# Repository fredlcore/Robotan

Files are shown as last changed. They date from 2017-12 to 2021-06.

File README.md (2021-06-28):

# Robotan
Die deutsche Version gibt es <A HREF="README_de.md">hier</A>.  

WiFi access to Zucchetti-based lawnmower robots (Ambrogio, Stiga, Herkules etc.)  
See a list of (partly still assumed) compatible robots <A HREF="Supported Models.md">here</A>.  
Some boards left over from a collective order are still available. Contact robotan (ät) code-it.de if you are interested (German or English).

<H2><A HREF="LICENSE.md">License</A></H2>
<H2><A HREF="Assembly Instructions.md">Building the Robotan board</A></H2>
<H2><A HREF="Installation.md">Installation</A></H2>
<H2><A HREF="Setup.md">Software Setup</A></H2>
<H2><A HREF="Configuration.md">Configuration</A></H2>
<H2><A HREF="Troubleshooting.md">Troubleshooting</A></H2>
<H2><A HREF="FAQ.md">Frequently Asked Questions (FAQ)</A></H2>

<B>Some screenshots:</B>  

<B>Web-based remote control:</B>

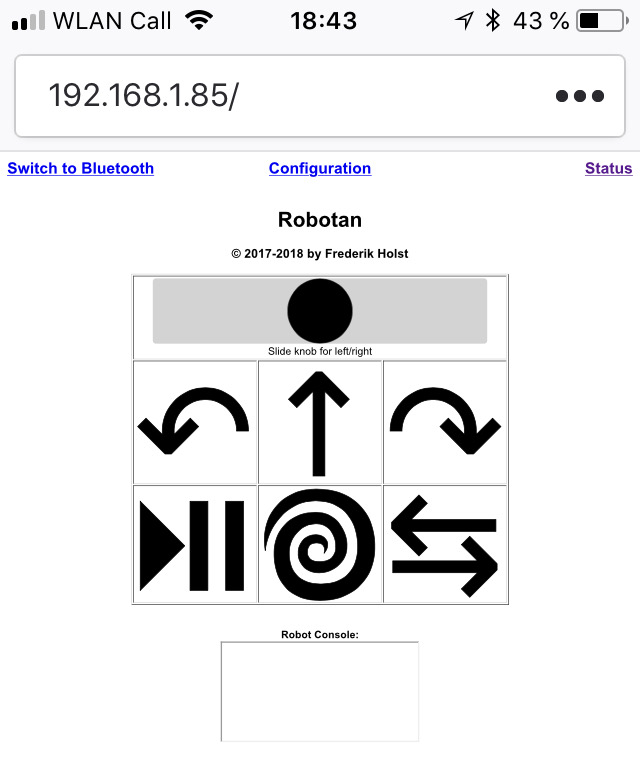
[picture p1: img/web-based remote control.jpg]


<B>Web interface with configuration and status information:</B>

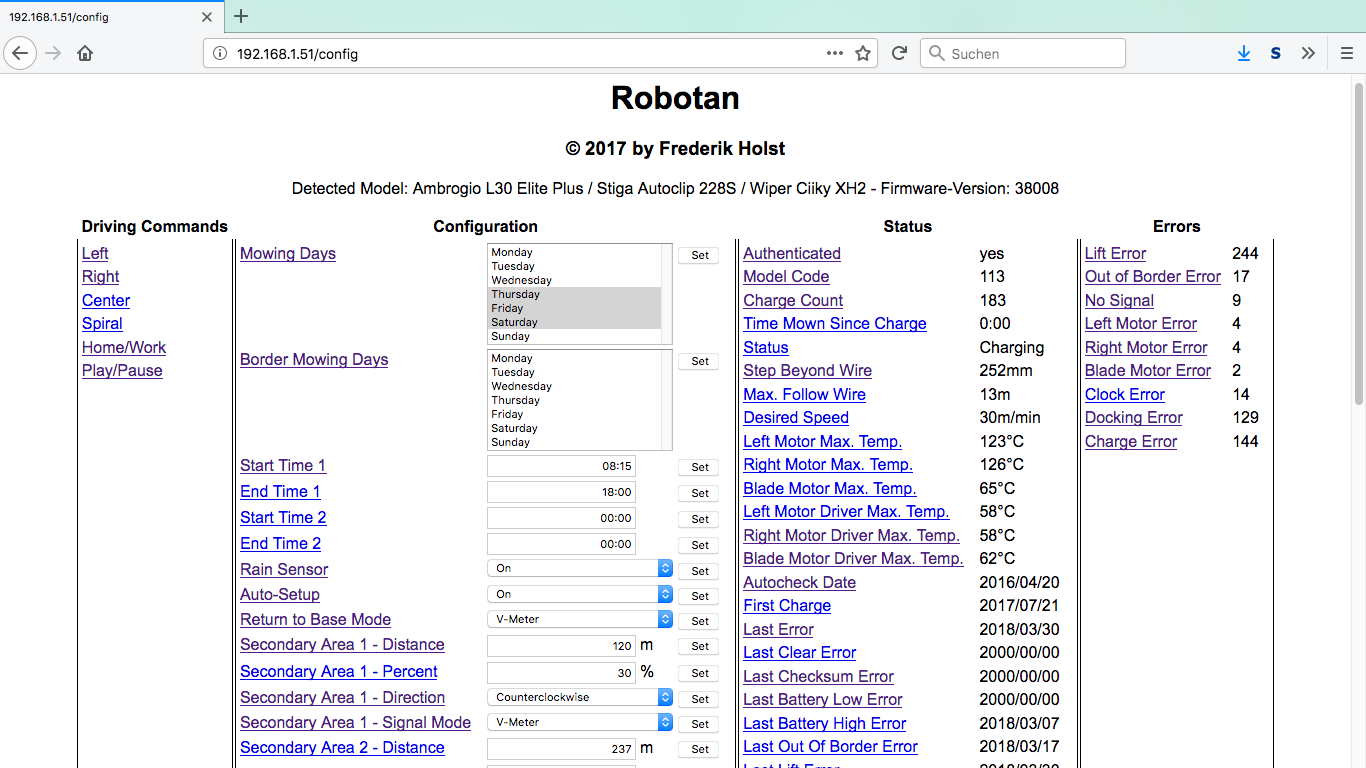
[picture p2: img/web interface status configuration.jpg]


<B>General settings (incl. GPS):</B>

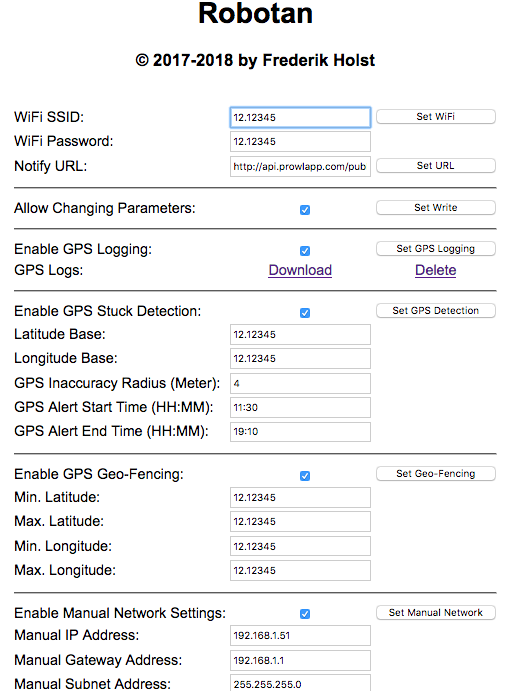
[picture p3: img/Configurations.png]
  

<B>Screencapture of realtime robot movements (new position polled every 10 seconds):</B>  
  
https://user-images.githubusercontent.com/24660955/123637079-e1455280-d81d-11eb-9b20-2d750a1a620e.mp4

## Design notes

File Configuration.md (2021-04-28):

<H2>Configuring Robotan</H2>
Die deutsche Version befindet sich <A HREF="Configuration_de.md">hier</A>.
<BR><BR>
To configure Robotan's options, go to<BR>
  <code>http://192.168.4.1/config</code>
<BR>
If you are asked for a login, the username is "Robotan" and the password is "Robotan88", unless you chose your own credentials during instalation.  
If Robotan is already connected to your own WiFi network, you'll have to use the IP address assigned to Robotan or try using the 
hostname "robotan" instead of the IP number. 
<H3>Configuring WiFi network</H3>
By default, Robotan sets up its own WiFi network called "Robotan" with the password "Robotan88". If you want to access your robot from 
within your own WiFi network, you can enter the name of your WiFi network at "WiFi SSID" and your WiFi's password at "WiFi Password".  
Then click on "Set WiFi" and wait a while. If your robot does not automatically connect to your own network, you can turn off the robot and
turn it on again after a few seconds.<BR>
<BR>
If Robotan cannot connect to your WiFi network, for example because the password is wrong or because it is too far away to pick up a signal, 
Robotan will fall back to setting up its own "Robotan" network mentioned above. However, it will try every five minutes to connect again to 
your WiFi network. This will ensure it will re-connect to your network even if it lost signal in a remote section of your garden.
<BR>
You also have the option to provide the Robotan module with a fixed IP address along with gateway, subnet and dns addresses in the configuration menu.

<H3>Configuring push notifications</H3>
Robotan can notify you in case the robot reports an error, for example when it gets stuck.  
To be able to send the notifications, Robotan must use your own WiFi network (see above). Robotan will call the URL defined at "Notify URL"
and add the reason for the notification (i.e. "Lift Error") at the very end, so you can call an URL and pass the reason as a parameter. If you don't want the error to be passed on, then just end your URL with a <code>#</code>. The reason text will still be appended, but the <code>#</code> will basically make the text being ignored in the URL.<BR>
<B>As of May 2020, only calls to https sites are supported!</B>
<H4>Example for using Prowl (Apple iPhone/iPad)</H4>
<A HREF="http://www.prowlapp.com">Prowl</A> is a notification app for iPhone and iPad. After you register, you can create an API key which 
you can send your notifications to. The URL for Robotan would look like this:<BR>
<code>https://api.prowlapp.com/publicapi/add?apikey=INSERT YOUR API KEY HERE&application=Robotan&event=</code>
<BR>
Take note of the end of the URL: The last parameter is "event=", so Robotan will add the reason for the notification there, so that the
final URL might end like "event=Lift Error"
<H4>Example for using SimplePush (Android)</H4>
<A HREF="http://www.simplepush.io">SimplePush</A> is a notification app for Android. After you've downloaded the app, you'll get a key which 
you can send your notifications to. The URL for Robotan would look like this:<BR>
<code>https://api.simplepush.io/send/INSERT YOUR KEY HERE/</code>. 
The error message will then be pushed to your Android device running the 
SimplePush app. Please take note that the URL must end with a <code>/</code>
after the key!
<BR>
<H4>Example for sending an e-mail via a PHP script</H4>
You can download and install the <A HREF="scripts/sendmail.php">sendmail.php script</A> on your own server and configure it to send an
e-mail through an e-mail service of your choice. Note: Only `https` addresses are supported!  
The script expects the parameter "error" to be sent via a GET request like this:<BR>
  <code>https://this-is-my-server.com/sendmail.php?error=Error-Message</code>
<BR>
Please make sure that the script runs smoothly before setting it up in Robotan by calling the script from your browser. If you receive
an e-mail from the script, you can use the URL in the Robotan configuration like this:
<BR>
  <code>https://this-is-my-server.com/sendmail.php?error=</code>
<BR>
Then click "Set URL" and Robotan will send out a notification each time an error occurs.

<H3>Configuring stuck detection</H3>
If you have installed a ADXL335 acceleration sensor, you can activate its use here which will provide a "stuck detection" for older robots who are not able to read the error status of the robot ("Steering only"). If you get false positives when the robot is mowing, play around with the sensitivity value a bit. Higher values lead to a greater tolerance, lesser values to a lower tolerance.

<H3>Configuring GPS functions</H3>
In the configuration menu, you have the following GPS-based options:  
<UL>
<LI>Enable GPS logging</LI>
GPS logs will be saved every 10 seconds into the device's flash memory until the size exceeds 1 MByte after which it will automatically be deleted. You have the option to download the logs in GPX format to be displayed for example on sites like <A HREF="http://www.gpsvisualizer.com/map_input">GPS Visualizer</A>.
<LI>Enable GPS stuck detection</LI>
This is useful for older robots which do not provide access to the error messages, like when the robot is stuck. This function will evaluate the (not 100% accurate) GPS position of the robot and determine whether the robot is stuck or not. The inaccuracy radius may help to prevent false positives. Alerts will only be sent during start and end time. Please note that these times are based on the UTC timezone (which is in summer two hours behind the rest of central Europe.  
The position of the base (garage) helps to prevent false positives when the robot is in the garage (and therefore looks as being 'stuck').  
<LI>Enable geo-fencing</LI>
You may provide coordinates of your garden here. Once the robot leaves these coordinates (e.g. because of theft) a message will be sent out with the current coordinates.
</UL>
<H3>GPIOs direct access</H3>
Via the URL <code>/gpio?x=y</code> the GPIO pins of the Wemos can be accessed directly, e.g. to control a relay shield, where <code>x</code> is the intenral number of the GPIO pin, and <code>y</code> is either 0 or 1, depending on whether the pin should be low or high.

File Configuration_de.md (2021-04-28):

<H2>Robotan konfigurieren</H2>
English version can be found <A HREF="Configuration.md">here</A>.
<BR><BR>
Um die Optionen von Robotan zu konfigurieren, ruft man folgende Adresse auf:
  `http://192.168.4.1/config`
<BR>
Wenn Du nach Zugangsdaten gefragt wirst, gib <code>Robotan</code> als Benutzernmane
und <code>Robotan88</code> als Passwort ein, wenn Du nicht bei der Installation Deine eigenen Zugangsdaten eingestellt hast. 
Falls Robotan bereits mit Deinem
WLAN-Netzwerk verbunden ist, musst Du die entsprechende IP-Adresse verwenden,
die Robotan zugewiesen wurde, oder den Hostnamen <code>robotan</code> statt
der IP-Adresse probieren.<BR>
<H3>WLAN-Netzwerk konfigurieren</H3>
Standardmäßig setzt Robotan sein eigenes WLAN-Netzwerk auf, das "Robotan" heißt 
und das Passwort <code>Robotan88</code> hat. Wenn Du Robotan aus Deinem eigenen
WLAN heraus erreichen möchtest, kannst Du den Namen des WLAN-Netzwerks unter
"WiFi SSID" und das WLAN-Passwort unter "WiFi Password" eingeben. Klicke dann
auf "Set WiFi" und warte einen Moment. Falls der Roboter sich nicht automatisch
mit Deinem WLAN verbindet, kannst Du den Roboter aus- und wieder anschalten.
Dann sollte er sich mit Deinem WLAN verbunden haben.
<BR><BR>
Falls Robotan sich nicht mit Deinem WLAN verbinden kann, weil z.B. das Passwort
falsch ist oder sich der Roboter außerhalb der WLAN-Reichweite befindet, wird
Robotan sein bereits erwähntes eigenes WLAN-Netzwerk "Robotan" aufspannen. Es
wird allerdings alle fünf Minuten probieren, sich wieder mit Deinem WLAN-Netzwerk
zu verbinden. Das gewährleistet, dass es sich wieder mit Deinem Netzwerk verbindet,
selbst wenn das Signal in einer entfernten Ecke Deines Gartens verloren gegangen
ist.<BR>  
Es gibt auch die Möglichkeit, dem Robotan-Modul im Konfigurationsmenü eine feste IP-Adresse, sowie Gateway-, Subnet- und DNS-Adressen zu vergeben.
<H3>Push Benachrichtigungen konfigurieren</H3>

Robotan kann Dich benachrichten, falls der Roboter einen Fehler aufweist, z.B.
wenn er sich festgefahren hat und angehoben werden muss.<BR>
Um Push-Benachrichtigungen versenden zu können, muss Robotan in Dein eigenes
WLAN eingebunden sein (s.o.). Robotan ruft im Falle eines Fehlers die URL auf,
die unter "Notify URL" angegeben ist und fügt dieser am Ende den Grund für die 
Meldung hinzu (z.B. "Lift Error" für den Fall, dass der Roboter feststeckt). 
Damit kann eine URL aufgerufen werden, die den Grund für die Meldung als Parameter
überträgt. Wenn Du nicht möchtest, dass die Fehlermeldung an das Script übertragen
wird, beende die URL einfach mit einem <code>#</code>. Der Grund für die Meldung
wird zwar weiterhin an die URL angehängt, aber das <code>#</code> sorgt dafür,
dass der Text nicht als Teil der URL interpretiert wird.<BR>
<B>Seit Mai 2020 sind nur noch Aufrufe von Seiten über https möglich!</B>

<H4>Beispiel: Benachrichtigung über Prowl (Apple iPhone/iPad)</H4>

<A HREF="http://www.prowlapp.com">Prowl</A> ist eine Benachrichtigungs App für
iPhone und iPad. Nachdem Du Dich dort registriert hast, kannst Du dort einen API
Schlüssel erzeigen, über den Du Benachrichtigungen an Dein Handy schicken kannst.
Die URL für Robotan würde folgendermaßen aussehen:<BR>
`https://api.prowlapp.com/publicapi/add?apikey=HIER DEN API SCHLÜSSEL EINTRAGEN&application=Robotan&event=`
<BR>
Beachte hierbei das Ende der URL: Der letzte Parameter ist "event=", woran 
Robotan den Benachrichtigungsgrund anhängen wird, so dass die endgülgtige URL
z.B. auf "event=Lift Error" enden könnte.

<H4>Beispiel: Benachrichtigung über SimplePush (Android)</H4>

<A HREF="http://www.simplepush.io">SimplePush</A> ist eine Benachrichtigungs App für
Android Geräte. Nachdem Du die App installiert hast, bekommst Du einen Schlüssel
angezeigt, über den Du Benachrichtigungen an Dein Handy schicken kannst.
Die URL für Robotan würde folgendermaßen aussehen:<BR>
`https://api.simplepush.io/send/HIER DEN SCHLÜSSEL EINTRAGEN/`
<BR>
Beachte hierbei das Ende der URL: Diese muss mit einem <code>/</code> hinter
dem Schlüssel enden!

<H4>Beispiel: E-Mail Versand über ein PHP Script</H4>

Du kannst das <A HREF="scripts/sendmail.php">sendmail.php script</A> auf Deinen
eigenen Server herunterladen und es so konfigurieren, dass es eine E-Mail über
einen E-Mail Server Deiner Wahl verschickt. Wichtig: Es werden nur Adressen mit `https` unterstützt!
Das Script erwartet den Parameter "error" über einen HTTP GET-Aufruf, z.B.
`https://this-is-my-server.com/sendmail.php?error=Error-Message`
<BR>
Bitte überprüfe, dass das Script fehlerfrei läuft, bevor Du es in Robotan 
einbindest, indem Du es vom Browser aus aufrufst. Wenn Du eine E-Mail von dem
Script erhälst, kannst Du die URL in der Robotan Konfiguration wie folgt 
einbinden:
<BR>
  `https://this-is-my-server.com/sendmail.php?error=`
<BR>
Dann klicke auf "Set URL" und Robotan wird jedes Mal, wenn ein Fehler auftritt,
eine Benachrichtigung versenden.

<H3>Stillstandserkennung konfigurieren (für ältere Roboter)</H3>
Wenn ein ADXL335 Beschleunigungssensor installiert ist, kann dieser hier aktiviert werden und die Stillstanderkennung bei älteren Robotern ermöglichen, die nicht auslesen können, ob ein Fehler vorliegt ("Steering only"). Falls es während des Fahrens des Roboters dennoch zu Fehlalarmen kommt, kann mit der Sensitivity-Einstellung möglicherweise eine Verbesserung erreicht werden. Höhere Werte führen zu einer größeren Toleranz, niedriegere Werte zu einer geringeren.

<H3>GPS-Funktionen konfigurieren</H3>
Im Konfigurationsmenü gibt es folgende GPS-Funktionen:
<UL>
<LI>Enable GPS Logging</LI>
Hiermit wird alle 10 Sekunden die GPS-Position in den Flash-Speicher des Robotan-
Moduls geschrieben, bis die Größe 1 MByte übersteigt (nach ca. 2 Tagen). 
Danach werden die Daten gelöscht und die Aufzeichnung beginnt von vorne. 
Es gibt die Möglichkeit, die Daten als GPX-Datei herunterzuladen und sie in einem
Dienst wie <A HREF="http://www.gpsvisualizer.com/map_input">GPS Visualizer</A> 
darstellen zu lassen.
<LI>Enable GPS Stuck Detection</LI>
Dies ist nützlich für ältere Roboter, bei denen keine Fehlermeldungen direkt 
abgerufen werden können, z.B. wenn sich der Roboter festgefahren hat.
Diese Funktion analyisert die (nie 100% genaue) GPS-Position des Roboters und 
versucht zu erkennen, ob der Roboter stillsteht oder nicht. Die "Inaccuracy"-Einstellung
kann helfen, Fehlalarme zu reduzieren, indem damit ein Radius festgelegt wird,
innerhalb dessen eine Bewegung noch als "Stillstand" gerechnet wird (3-4 Meter können hier sinnvoll sein).
Meldungen werden nur innerhalb der angegebenen Zeiten versendet. Bitte beachte,
dass diese Zeiten in der UTC-Zeitzone eingegeben werden müssen, die im Sommer
zwei Stunden hinter der Zeit in den meisten Staaten Mitteleuropas liegt.
Die Position der Basis (Garage) kann angegeben werden, um zu verhindern, dass
ein geparkter Roboter eine Warnmeldung erzeugt.  
<LI>Enable Geo-Fencing</LI>
Hier können die äußeren Koordinaten des Grundstücks angegeben werden. Wenn sich
der Roboter außerhalb dieser Koordinaten aufhält (z.B., weil er gerade gestohlen wird), dann wird eine Nachricht mit den momentanen Koordinaten versendet.
Bitte beachten: Auch hier kann es durch GPS-Ungenauigkeiten zu Fehlermeldungen kommen, wenn die Grundstückskoordinaten exakt eingegeben werden.
</UL>
<H3>GPIOs Direktzugriff</H3>
Über die URL <code>/gpio?x=y</code> können die GPIO-Pins des Wemos direkt angesprochen werden, z.B. um ein Relay-Shield anzusteuern
o.ä. Dabei ist <code>x</code> die interne Nummer des GPIO Pins und <code>y</code> entweder 0 oder 1, je nachdem, ob der Pin auf low oder high gesetzt werden soll.

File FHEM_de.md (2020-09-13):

<H2>Einbindung in FHEM</H2>
English version can be found <A HREF="FHEM.md">here</A>.
<BR>
<H3>Robotan-Modul in FHEM einbinden</H3>
Um Robotan in FHEM einzubinden, muss das Modul 98_Robotan.pm in das Verzeichnis <code>./opt/FHEM</code> unterhalb der FHEM-Installation
kopiert werden.<BR>
Dann erfolgt die Einbindung in FHEM mit<BR>
<code>define Ciiky Robotan:Robotan88@192.168.1.51 300</code><BR>
Damit wird das Gerät "Ciiky" angelegt, mit den Standardzugangsdaten (Benutzername Robotan, Passwort Robotan88), das auf die IP
192.168.1.51 eingestellt ist. Der Abfrageintervall wird auf 300 Sekunden festgelegt, also alle fünf Minuten.<BR>
<BR>
<H3>Modulkonfiguration</H3>
<code>Left</code>, <code>Right</code>, <code>Straight</code> - Lässt den Roboter links bzw. rechts bzw. gerade fahren.<BR>
<code>Spiral</code> - lässt den Roboter temporär in Spiralform mähen<BR>
<code>Home/Work</code> - lässt den Roboter je nach Status aus bzw. zurück in die Station fahren.<BR>
<code>Play/Pause</code> - lässt den Roboter in bzw. aus dem Pause-Modus gehen. Der Pause-Modus ist Voraussetzung, um Parameter im Roboter zu ändern, u.a. auch die Mähzeiten und -tage.<BR>
<code>Start_Time_1</code> - Beginn der ersten Mähzeit<BR>
<code>End_Time_1</code> - Ende der ersten Mähzeit<BR>
<code>Start_Time_2</code> - Beginn der zweiten Mähzeit<BR>
<code>End_Time_2</code> - Ende der zweiten Mähzeit<BR>
<BR>
<code>Mowing_Days</code> - Setzt direkt die Wochentage im Roboter, an denen der Rand gemäht werden soll.<BR> 
<code>General_Mowing_Days</code> - Standard-Mäh-Tage; kann kann von Funktionen verwendet werden, um z.B. nach <code>Mow_Today</code> die Standard-Einstellungen wieder herzustellen.<BR>
<code>Border_Mowing_Days</code> - Setzt direkt die Wochentage im Roboter, an denen der Rand gemäht werden soll.<BR>
<code>General_Border_Mowing_Days</code> - Standard-Randmäh-Tage; kann von Funktionen verwendet werden, um z.B. nach <code>Mow_Today</code> die Standard-Einstellungen wieder herzustellen.<BR>
<code>Mow_Today</code> - <code>1</code> fügt den heutigen Tag den Mähtagen hinzu, <code>0</code> entfernt ihn. Die übrigen Mähtage werden aus <code>General_Border_Mowing_Days</code> (also dem in FHEM hinterlegten Standard) ausgelesen, nicht aus dem Roboter direkt. 
<H3>Beispieleinbindungen</H3>
<B>Mähzeiten entsprechend des Tageslichts anpassen:</B><BR>
<pre>
define di_Ciiky_Daylight_Mowing DOIF ([01:10]) ## execute at 01:10 am
((set Ciiky Start_Time_1 {(sunrise_abs(3600, "08:15"))}), ## set start time to one hour after sunrise, but not earlier than 08:15 am
(set Ciiky End_Time_1 {(sunset_abs(-3600, "", "20:00"))})) ## set end time to one hour before sunset, but not later than 8pm
</pre>
<BR>
<B>Kein Mähen, wenn schlechtes Wetter vorhergesagt wird:</B><BR>
Benötigt das Modul PROPLANTA, hier am Beispiel der Postleitzahl 29439<BR>
<pre>
define Wetter PROPLANTA 29439 de
define di_No_Mow_When_Bad_Weather DOIF ([Wetter:fc0_tempMax] < 12 ## check if weather today is bad, i.e. rain or less than 12°C
or ([Wetter:fc0_rain] > 1))
(set Ciiky Mow_Today 0) ## then do not mow today
</pre>
<BR>
<B>Nachts wieder auf Standard-Mähtage zurücksetzen:</B><BR>
<pre>
define di_Ciiky_Set_Standard_Mowing_Times DOIF ([01:05]) ## execute at 01:05 am
(set Ciiky Mowing_Days {(AttrVal("Ciiky","General_Mowing_Days",""))}, ## reset mowing days with value from General_Mowing_Days
set Ciiky Border_Mowing_Days {(AttrVal("Ciiky","General_Border_Mowing_Days",""))}) ## reset border mowing days with value from General_Border_Mowing_Days
</pre>

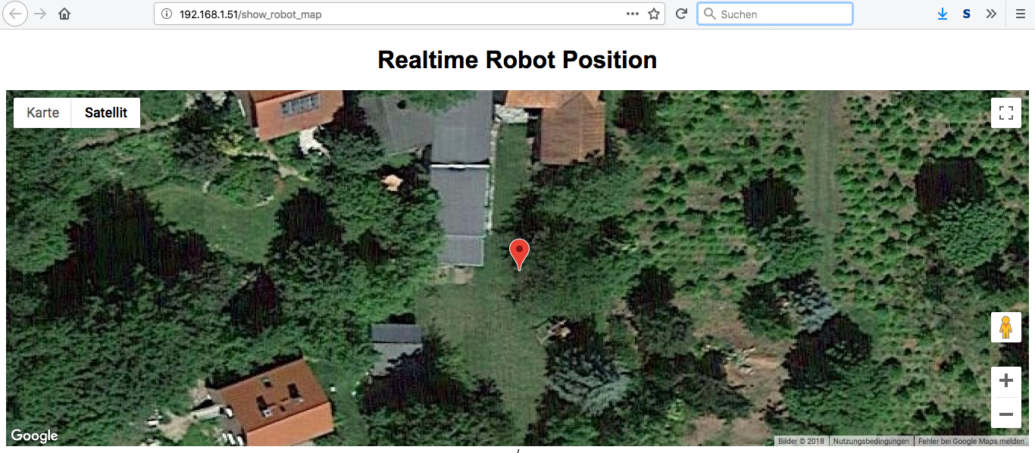
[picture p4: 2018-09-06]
img/Robot-Realtime-Position.png

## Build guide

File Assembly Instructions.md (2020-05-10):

<H2>Assembly Instructions</H2>
Die deutsche Version findet man  <A HREF="Assembly Instructions_de.md">hier</A>.  
<BR><BR>
To assemble the Robotan board, you'll need the <A HREF="schematics">plain board</A> itself plus:  
<BR>
<UL>
<LI>1 x Wemos D1 Mini
<LI>1 x MAX 3232 CPE DIP 16 RS232/TTL converter
<LI>1 x 9 pin male serial connector
<LI>5 x 0.1µF capacitators
<LI>1 x 470µF capacitator
<LI>2 x 8 pin header
<LI>2 x 8 pin socket
<LI>optionally: 1 x <A HREF="https://amzn.to/2ZaNa4P">HC-05 Bluetooth module</A> (HC-06 also works)
<LI>optionally: 1 x <A HREF="https://amzn.to/2JXdzQ2">u-blox NEO-6 GPS module</A> (or compatible)
<LI>optionally: 1 x <A HREF="https://amzn.to/2MoVvjT">ADXL335 acceleration sensor</A> (analogue, with X/Y/Z output pins) for older robots for stuck detection
<LI>optionally: 1 x <A HREF="https://amzn.to/3184fOL">KY-003</A> hall effect sensor (digital, active low) for older robots for stuck detection
<LI>optionally: 1 x <A HREF="https://amzn.to/2MqvkJP">strong magnet (N52)</A> for the hall effect sensor
<LI>optionally: 1 x Piezo buzzer CPM 121 (for alarm beeps when robot is outside GPS boundaries)
  </UL>
Except for the Wemos D1 Mini and the extension modules/sensors, you can find a list of items at <A HREF="https://www.reichelt.de/my/1409494">Reichelt</A>.  
<BR>
Some boards from a collective order are still available. Contact robotan (ät) code-it.de if you are interested (German or English).
<BR><BR>
To assemble the board, proceed as follows:
<BR>

1. Solder the MAX 3232 CPE on the board.

2. Solder the five 0.1µF capacitators on the board at the designated spots

3. Solder the 470µF capacitator on the board at the designatet spot - watch the polarity!

4. Solder the two 8 pin sockets to the Wemos D1 mini and the two 8 pin headers on the Robotan board.

5. Solder the serial connector to the board. You might have to bend the two adjacent capacitators a bit.

6. Plug the Robotan board on top of the Wemos D1 Mini. The serial connector of the Robotan board must be on the same side as the Micro USB 
connector of the Wemos D1 Mini.

7. If you need to flash the firmware via USB, you have to unplug the board and the Wemos first. This usually only applies to the first flashing process, because afterwards you can use the web-based flashing feature which is not affected by this.

8. If you want to add the u-blox GPS module, you can solder the pins like this:  
VCC <-> 3V3  
GND <-> G  
TX <-> D7  
Do not connect the RX line of the module as it is not used and might interfere with the Wemos D1 Mini board.  
If you connect the piezo buzzer to D2 (+) and GND (-), an SOS beep will turn on once the robot has left the permissible GPS coordinates.<BR><BR>
On the newer version of the board, the pins in the parallel row marked as "GPS" can be used. Opposite of D6 is a GND pin so that the GPS module can be attached 1:1. Pin D0 is additionally located at the top right of the baurd so that a buzzer can be soldered in there direclty.

9. If you want to add the  ADXL335 acceleration sensor in older robots for detecting whether the robot is stuck, connect the pins one to one like this:  
VCC <-> 3V3  
GND <-> G  
X/Y/Z (one of them) <-> A0  
Use that axis pin on the ADXL335 that best matches the horizontal movement axis of the robot. This depends on where and in which direction you have attached the sensor inside the robot. On the newer version of the board, the respective pins can be found in the parallel row named "ACC". The pins between 3V3 and GND are all connected to A0.  
To reduce or at best eliminate false alarms on older robots when the robot is back in its base, you can use a Hall Effect Sensor KY-003 in combination with a strong magnet. Connect ths pins like this:
VCC <-> 5V  
GND <-> G  
SIG/OUT <-> D1  
Magnet and sensor should be placed in a way that there is only a very small distance between them when the robot is in its base (2-3 cm), this is possible for example by placing the sensor directly on/below the ground plate of the chassis and then place the magnet on the ground below, or to place the sensor at the front of the robot and the magnet attached to the charging elements. You might have to try a bit to find the most reliable position!   

10. If you want to add the HC-05 Bluetooth module, you can solder the pins one 
to one like this, newer versions of the board have a parallel row labelled as "BLUETOOTH" which are connected the same way:  
5V <-> 5V  
GND <-> G  
TX <-> D4  
RX <-> D3  
For modules with six pins, make sure you only connect the four center ones 
(5V, GND, RX and TX)!  
To configure the HC-05, see the manual or try the `RobotanBT.ino` which should
be able to configure the Bluetooth module correctly. You have to put the module
into programming mode first by connecting the 5V and EN pins on the module 
while powering up. Better modules have a microswitch which you just need to
press alternatively.  
<H3>Done :-)!</H3>
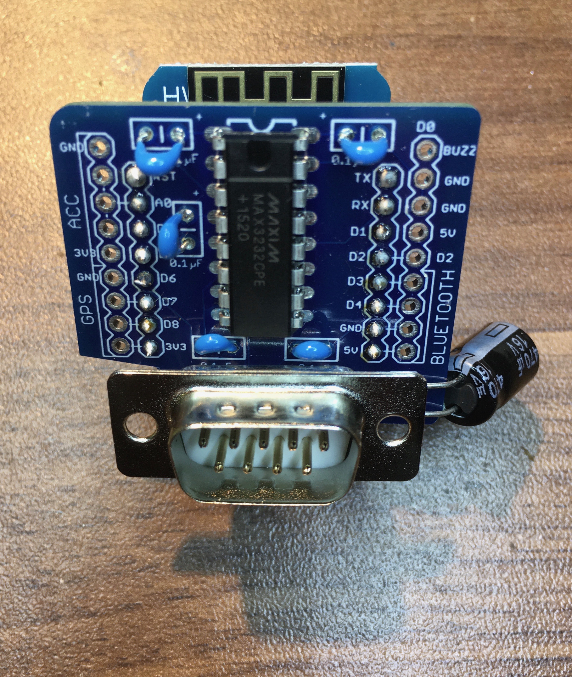
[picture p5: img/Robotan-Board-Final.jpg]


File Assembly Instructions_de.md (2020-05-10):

<H2>Zusammenbau des Robotan Boards</H2>
English version can be found <A HREF="Assembly Instructions.md">here</A>.
<BR><BR>
Um das Robotan Board zusammenzubauen, benötigt man das 
<A HREF="schematics">unbestückte Board</A> sowie:  
<BR>
<UL>
<LI>1 x Wemos D1 Mini
<LI>1 x MAX 3232 CPE DIP 16 RS232/TTL Konverter
<LI>1 x 9-poliger serieller Stecker (männlich)
<LI>5 x 0.1µF Kondensatoren
<LI>1 x 470µF Kondensator
<LI>2 x 8 Pin Steckerleiste
<LI>2 x 8 Pin Buchsenleiste
<LI>optional: 1 x <A HREF="https://amzn.to/2ZaNa4P">HC-05 Bluetooth Modul</A> (HC-06 auch möglich)
<LI>optional: 1 x <A HREF="https://amzn.to/2JXdzQ2">u-blox NEO-6 GPS Modul</A> (oder kompatibel)
<LI>optional: 1 x <A HREF="https://amzn.to/2MoVvjT">ADXL335 Beschleunigungssensor</A> (mit analogem X/Y/Z Ausgangspins) für ältere Roboter zur Stillstandserkennung
<LI>optional: 1 x <A HREF="https://amzn.to/3184fOL">KY-003 Halleffektsensor</A> (digital, active low) für ältere Roboter zur Stillstandserkennung
<LI>optional: 1 x <A HREF="https://amzn.to/2MqvkJP">starker Magnet (N52)</A> für den Halleffektsensor
<LI>optional: 1 x Piezo Summer CPM 121 (für Alarmierung, wenn der Roboter außerhalb der zulässigen GPS-Koordinaten ist)
  </UL>
Außer dem Wemos D1 Mini und den Erweiterungsmodulen/-sensoren finden sich alle Bauteile in dieser Liste bei <A HREF="https://www.reichelt.de/my/1409494">Reichelt</A>.

Dann wie folgt vorgehen:
<BR>

1. Die zwei 8 Pin Buchsenleisten auf den Wemos D1 mini löten und die zwei 8 Pin Steckerleisten auf das Robotan Board.

2. Dann den MAX 3232 CPE auf das Board löten.

3. Dann die fünf 0.1µF Kondensatoren an den markierten Stellen auf das Board löten.

4. Dann den 470µF Kondensator an der markierten Stelle auf das Board löten, dabei unbedingt die Polarität beachten!

5. Dann den seriellen Stecker auf das Board löten. Ggf. muss man die zwei angrenzenden Kondensatoren etwas biegen.

6. Dann das Robotan Board auf den Wemos D1 Mini stecken. Dabei muss der serielle Stecker auf der selben Seite sein, wie der Micro-USB-Anschluss des Wemos D1 Mini.

7. Wenn die Firmware per USB geflasht werden muss (was in der Regel nur bei der allerersten Installation der Fall ist), muss dafür das Board wieder vom Wemos gelöst werden. Bei allen Flash-Vorgängen über die Weboberfläche ist das nicht nötig.

8. Das optionale GPS-Modul kann wie folgt an das Robotan-Modul 
angelötet werden: 
VCC <-> 3V3  
GND <-> G    
TX <-> D7  
Den RX-Pin des GPS-Moduls nicht verbinden, da es den Boot-Prozess des Wemos D1 Mini Boards beeinflussen könnte.  
Wenn ein Piezosummer mit Pin D0, (+) und GND (-) verbunden wird, ertönen SOS-Piepser, wenn sich der Roboter außerhalb der zulässigen GPS-Koordinaten befindet.<BR><BR>
Bei der neuen Version des Boards können die entsprechenden Pins in der parallelen Anschlussreihe verwendet werden, die mit "GPS" beschriftet sind. Dort ist gegenüber von D6 ein Masse-Pin, so dass das Modul dort 1:1 angeschlossen werden kann. Pin D0 ist zusätzlich an der rechten Stirnseite des Boards ausgeführt, so dass hier ein Summer direkt angelötet werden kann. 

9. Der optionale Beschleunigungssensor ADXL335, der die Stillstandserkennung bei älteren Robotern verbessert, muss wie folgt angeschlossen werden:  
VCC <-> 3V3  
GND <-> G  
X/Y/Z (einer davon) <-> A0  
Dabei ist die Achse zu wählen, die nach Einbau des Sensors die horizontale Bewegungsachse am besten abbildet. 
Bei der neueren Version des Boards sind die entsprechenden Pins in der parallelen Anschlussreihe bei der Beschriftung "ACC" zu finden. Die zwischen dem 3V3- und Masse-Pin liegenden Anschlüsse sind alle auf A0 geschaltet.<BR>
Um bei älteren Robotern einen Fehlalarm bei Stillstand in der Basis zu vermeiden, kann mit dem Hall Effekt Sensor KY-003 in Kombination mit einem starken Magneten die Erkennung der Basis ermöglicht werden. Dabei muss die Verbindung wie folgt hergestellt werden:  
VCC <-> 5V  
GND <-> G  
SIG/OUT <-> D1  
Magnet und Sensor sind dann so zu platzieren, dass dazwischen ein möglichst kleiner Abstand erzielt wird (2-3 cm), möglich ist dies z.B., wenn der Sensor direkt an/unter der Bodenplattte befestigt wird und der Magnet darunter, oder an der Frontseite des Roboters und der Magnet an der Ladestation. Hier ist Ausprobieren gefragt!    

10. Das optionale Bluetooth-Modul kann eins-zu-eins an das Robotan-Modul 
angelötet werden, bei der neuen Version des Boards können die entsprechenden Pins in der parallelen Anschlussreihe verwendet werden, die mit "Bluetooth" beschriftet sind:  
5V <-> 5V  
GND <-> G    
TX <-> D4  
RX <-> D3  
Bei Modulen mit sechs Pins unbedingt darauf achten, dass nur die mittleren vier 
Pins (also 5V, GND, RX und TX) verbunden werden!  
Um das Bluetooth-Modul zu konfigurieren, bitte die entsprechende Anleitung
zu Rate ziehen oder den `RobotanBT.ino` Sketch probieren, der das Modul im 
Idealfall ebenfalls korrekt konfiguriert. Dazu muss das Modul in den Programmier-
Modus versetzt werden. Dies geschieht beim Einschalten der Stromzufuhr des
Moduls entweder durch das Kurzschließen der Pins 5V und EN oder durch Drücken 
eines Microschalters.

<H3>Fertig :-)!</H3>


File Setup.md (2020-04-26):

<H2>Installing and updating the Robotan firmware</H2>
Die deutsche Version befindet sich <A HREF="Setup_de.md">hier</A>.
<BR><BR>
The procedures of installing and updating are slightly different, but once a firmware is installed, you can always use the browser-based
update function described further below.

<H3>Installing the firmware for the first time</H3>
If you want to install the Robotan firmware on a fresh Wemos D1 device which does not have a firmware installed, 
you have follow the following steps:

1. Download and install the Arduino IDE as well as the ESP8266 core as described <A HREF="https://github.com/esp8266/Arduino#installing-with-boards-manager">here</A>.

2. In the Arduino IDE, set the following parameters in the "Tools" menu:
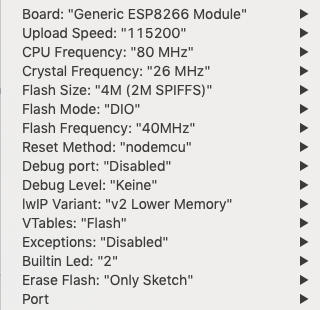
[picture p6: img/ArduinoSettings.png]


3. Connect the Wemos D1 with your computer via USB but WITHOUT THE ROBOTAN BOARD ATTACHED and flash the <A HREF="RobotanSetup/RobotanSetup.ino">RobotanSetup.ino</A>.  
Before flashing, you may set individual credentials for your personal WiFi 
network (variables WLAN_local_SSID and WLAN_local_password) as well as for the 
username and password for the webinterface (variables http_username and 
http_password). These will then be stored in the module and used instead of the 
default ones mentioned below.

4. Now a minimal browser-based firmware update program is installed on the Wemos D1 and you can proceed with the updating procedures explained below.

<H3>Updating the firmware via the web browser</H3>
Updating only works if a Robotan firmware or the RobotanSetup.ino has been installed before! 
If that is not the case, please go back to the beginning of this page and install the RobotanSetup.ino first.
Otherwise follow these steps:

1. Download the most recent <A HREF="Robotan.ino.bin">Robotan.ino.bin</A> and save it on your computer.

2. Connect to the robot's WiFi network. The default network name is "Robotan" and the WiFi password is "Robotan88" (without quotation marks).
If you have configured Robotan to use your existing WiFi network, you have to be connected to that WiFi network instead.

3. Open the following URL if you use the Robotan default WiFi, otherwise replace the IP number with the IP the Robotan has in your local WiFi network:  
`http://192.168.4.1:8080/update`  
If you are asked for a login, the defautl username is "Robotan" and the password is "Robotan88". If you have configured your own credentials, of course you have to use them instead. 

4. Under "Firmware-Update", please browse to the Robotan.ino.bin you have downloaded before and click "Update". Do not use the "Update Filesystem" upload option, if present.

5. If the upload was successful, Robotan will reboot and after a short while you should be able to access the Robotan web interface at
`http://192.168.4.1`.
If you have cofigured Robotan to use your own WiFi network, these settings will still be there, so you can access the web interface via
the IP number you have used before.  
If you are asked for a login, the username is "Robotan" and the password is "Robotan88", unless you have configured your own individual username/password. 
<BR><BR>
<B>Please note: Each time you insert the Robotan board into your robot, 
you will be asked for a PIN password on your robot.</B> <BR>
This is the PIN you have assigned your robot during setup and is by default 0000.<BR>
<B>Unless the robot is authenticated, you won't be able to control it!</B><BR>
In case you do not enter the PIN quickly enough, you might have to turn the 
robot off and on again, as it checks for authentication soon after powering on.

<H3>Done :-)!</H3>

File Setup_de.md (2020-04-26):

<H2>Installieren und Updaten der Robotan Firmware</H2>
English version can be found <A HREF="Setup.md">here</A>.
<BR><BR>
Die Prozeduren für das Installieren und Updaten der Robotan Firmware unterscheiden
sich leicht, aber sobald einmal eine Robotan Firmware installiert ist, kann man
immer die browserbasierte Update-Funktion verwenden, die weiter unten beschrieben 
wird.

<H3>Erstmalige Installation der Firmware</H3>

Wenn Du die Robotan Firmware auf einem neuen Wemos D1 Mini installieren möchtest,
auf dem bisher noch keine Robotan Firmware installiert wurde, musst Du die folgenden
Schrite durchführen:

1. Herunterladen und Installieren der Arduino IDE sowie des ESP8266 Cores wie <A HREF="https://github.com/esp8266/Arduino#installing-with-boards-manager">hier</A> beschrieben.

2. In der Arduino IDE müssen die folgenden Parameter im "Werkzeuge" Menü eingestellt
werden:


3. Verbinde den Wemos D1 über USB mit Deinem Computer ABER OHNE DAS ROBOTAN BOARD und flashe den Sketch
<A HREF="RobotanSetup/RobotanSetup.ino">RobotanSetup.ino</A>.  
In dieser Datei können vorher noch bei Bedarf individuelle Zugangsdaten für das 
WLAN (Variablen WLAN_local_SSID und WLAN_local_password) sowie für den Zugang 
zum Webinterface (Variablen http_username und http_password) konfiguriert 
werden. Diese werden dann im  Modul gespeichert und anstatt der später 
beschriebenen Standardwerte verwendet.

4. Danach ist eine minimale Browser-Upload Firmware auf dem Wemos D1 installiert 
und Du kannst mit dem Update-Prozess wie folgt fortfahren.

<H3>Updaten der Firmware über den Webbrowser</H3>

Das Updaten der Firmware funktioniert nur, wenn vorher eine Robotan Firmware
oder die RobotanSetup.ino installiert war! Wenn das nicht der Fall ist,
gehe bitte zurück zum Anfang dieser Seite und installiere zuerst die 
RobotanSetup.ino. Ansonsten folge diesen Schritten:

1. Lade die aktuelle <A HREF="Robotan.ino.bin">Robotan.ino.bin</A> herunter und
speichere sie auf Deinem Computer.

2. Verbinde Dich mit dem WLAN-Netzwerk des Roboters. Der Standardname des 
WLANs lautet <code>Robotan</code> und das Passwort <code>Robotan88</code>.
Wenn Du Robotan so konfiguriert hast, dass er Teil Deines WLAN-Netzwerks ist,
musst Du natürlich mit diesem Netzwerk verbunden sein.

3. Öffne die folgende URL, wenn Du das Standard-WLAN von Robotan verwendest,
andernfalls ersetze die IP-Nummer mit der IP, die Robotan in Deinem WLAN 
verwendet:  
`http://192.168.4.1:8080/update`  
Wenn Du nach Zugangsdaten gefragt wirst, lautet der Benutzername <code>Robotan</code> und das Passwort <code>Robotan88</code>, es sei denn Du hast bei der Installation Deine eigenen Werte angegeben.

4. Wähle unter "Firmware-Update" die Robotan.ino.bin aus, die Du vorher heruntergeladen
hast und klicke auf "Update". Bitte nicht unter "Filesystem-Update" hochladen, falls dies angezeigt werden sollte!

5. Wenn der Upload erfolgreich war, wird Robotan neu starten und nach einer 
kurzen Weile solltest Du das Robotan Webinterface unter 
`http://192.168.4.1` aufrufen können. Wenn Du Robotan so konfiguriert
hast, dass er Teil Deines WLANs ist, bleiben diese Einstellungen auch nach einem
Update erhalten, so dass Du das Webinterface über die IP-Adresse aufrufen kannst,
die Robotan in Deinem WLAN bekommen hat.<BR>
Wenn Du nach Zugangsdaten gefragt wirst, lautet der Benutzername <code>Robotan</code>
und das Passwort <code>Robotan88</code>, falls Du keine eigenen Werte bei der Installation angegeben hast..
<BR><BR>
<B>Bitte beachte: Jedes Mal, wenn das Robotan Board in Deinem Mähroboter
eingesteckt wird, fragt der Mäher nach einem PIN Passwort!</B> <BR>
Das ist die PIN, die bei Installation des Mähers im Setup eingegeben wurde und 
ist standardmäßig 0000.<BR>
<B>Ohne die Eingabe der PIN kann der Roboter nicht gesteuert werden!</B> <BR>
Falls die PIN nicht schnell genug nach dem Start eingegeben wurde, muss der Roboter
noch einmal aus- und wieder angeschaltet werden, um beim Hochfahren den neuen
Status zu erkennen. eine erneute PIN-Eingabe ist dann i.d.R. nicht mehr nötig.
<H3>Fertig :-)!</H3>

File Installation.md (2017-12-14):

<H2>Installation</H2>
Die deutsche Version befindet sich <A HREF="Installation_de.md">hier</A>.  
<BR><BR>
Installaion of the Robotan board is pretty straightforward, but please take note that because this is not an official Zucchetti product,
YOU WILL LOSE YOUR WARRANTY. So please proceed only if you are aware of this fact!

Photos shown are from a Herkules Wiper Ciiky XH2 (same model as Ambrogio L30 or Stiga Autoclip 228S), so if you have a different model,
the location of the screws might be different. Ask your dealer or in a forum if you are not sure!

<H3>Opening the robot</H3>
First, turn the robot around so you can see the bottom and locate the two plastic covers at the bottom of the robot which cover the bottom screws:
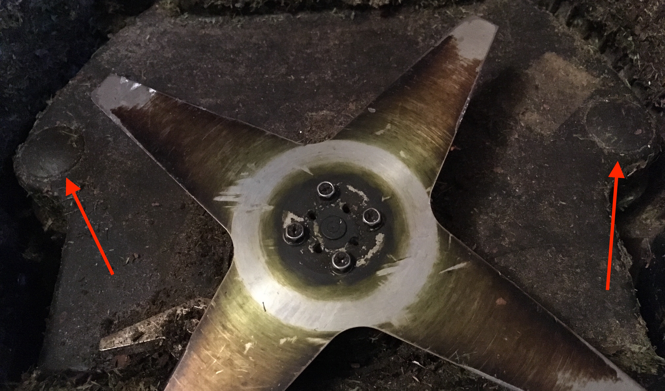
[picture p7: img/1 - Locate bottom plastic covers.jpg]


Then remove these plastic covers with a flat screwdriver. Be extra careful not to cut yourself by touching the robot blades!
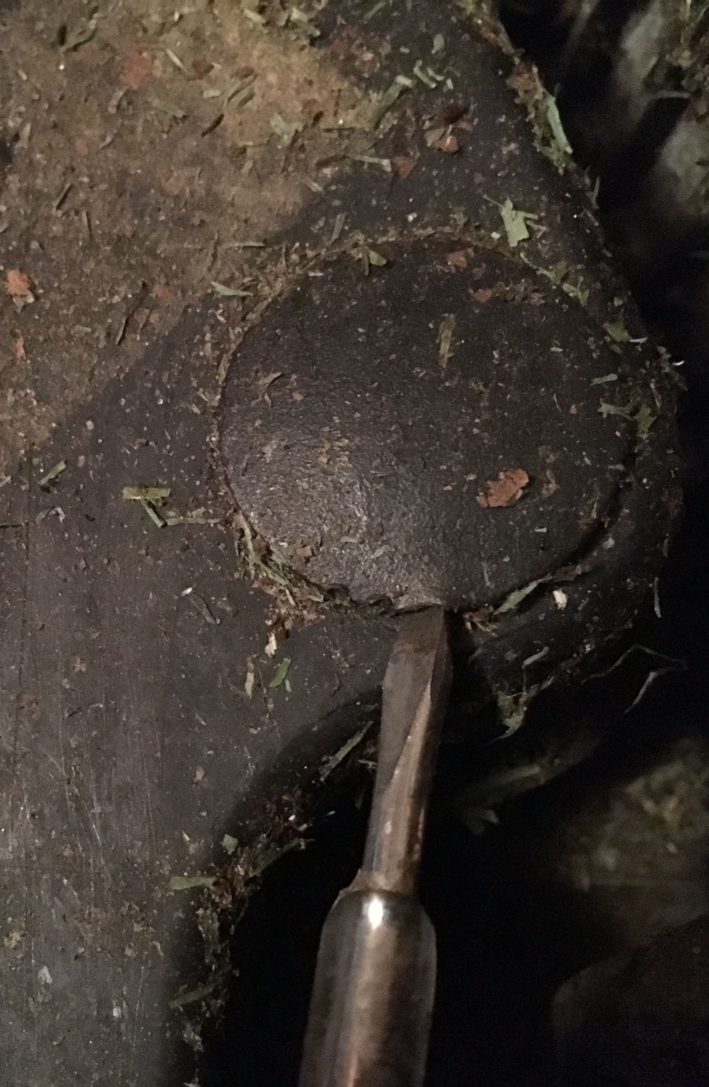
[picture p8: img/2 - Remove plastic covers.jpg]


Now remove the two screws. They might not come out completely, that's ok.
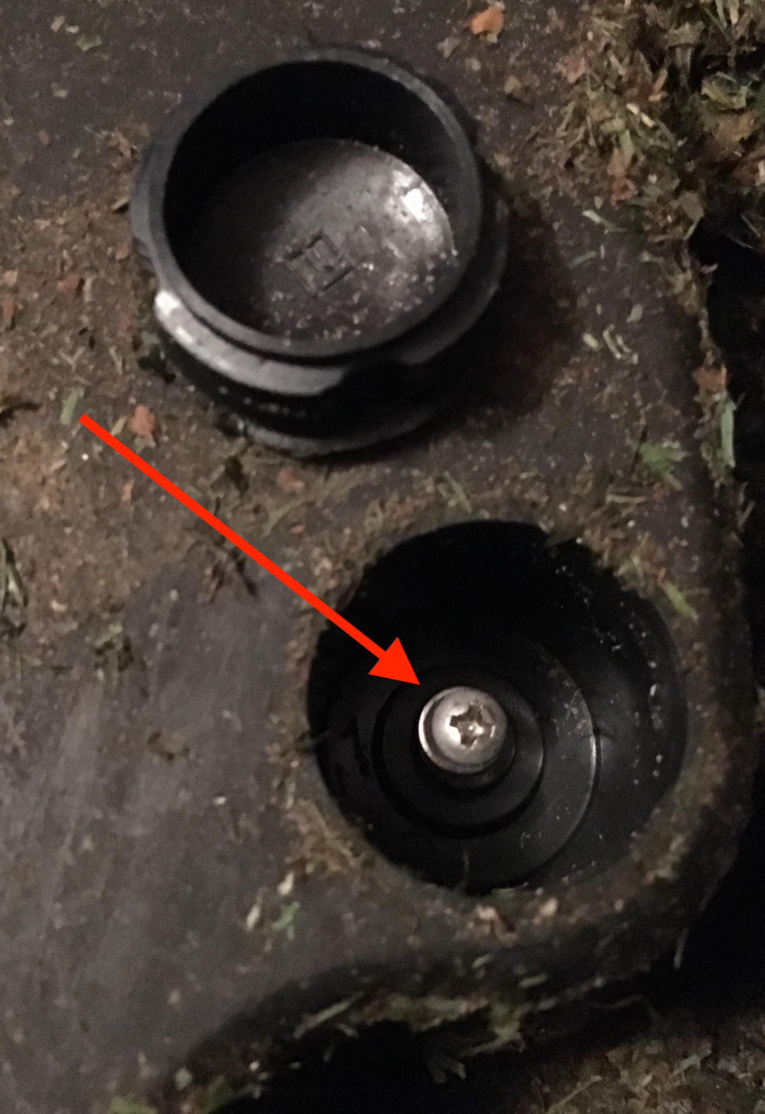
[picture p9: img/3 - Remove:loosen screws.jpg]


Now turn the robot back around and locate the two Torx screws at the back of the robot and remove them.
They might not come out completely, but that's ok. You just need to be able to press the two buttons above the screws to lift the cover.
Take care not to open the cover too wide, otherwise some of the connector cables will come off. Opening it 5-10 centimeters is enough.
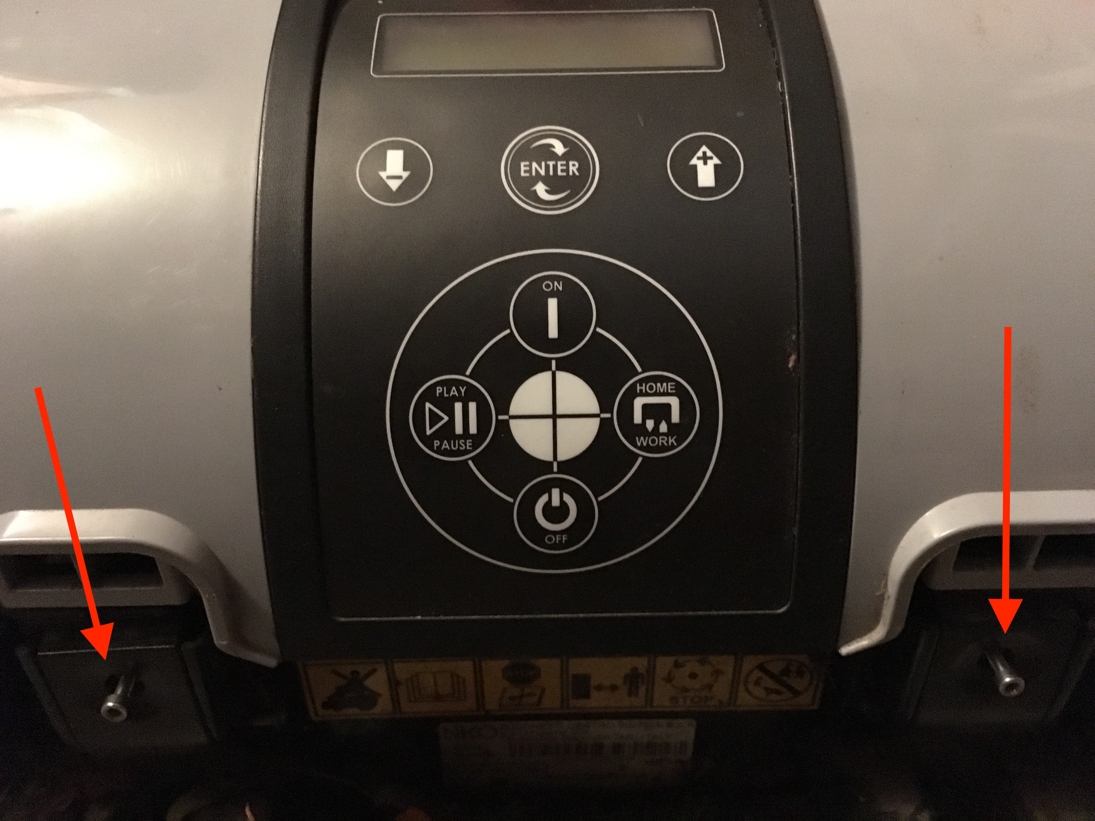
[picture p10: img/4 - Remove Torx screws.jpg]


<H3>Installing the Robotan module</H3>

Locate the bluetooth module if installed, otherwise proceed to the next step. Remove the bluetooth module and keep it in a safe place.
You'll need it in the future in case you want to do a firmware update of the robot via bluetooth.  
To remove the module, you have to remove two screws which fixate the module to the robot's mainboard. They are right under the round holes
of the module (see blue arrows):
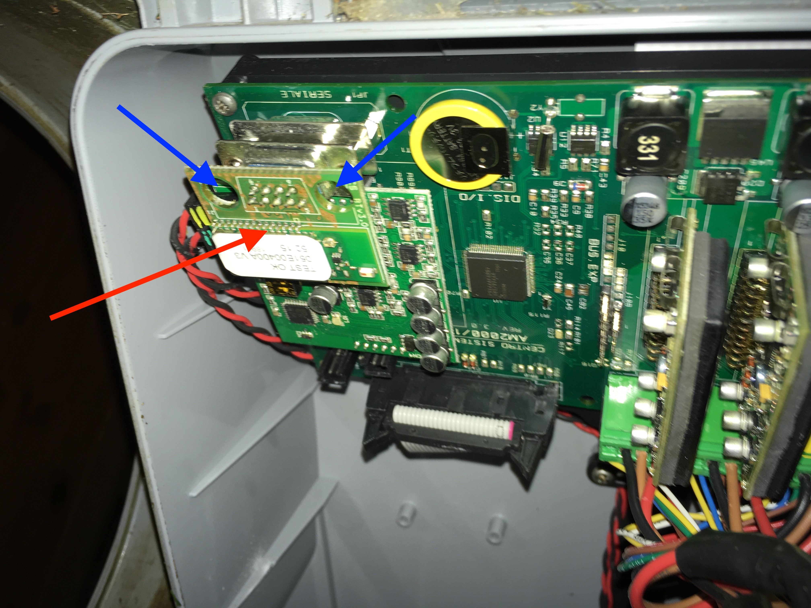
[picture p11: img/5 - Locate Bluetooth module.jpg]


Locate the empty serial port and insert the Robotan module. If the module does
not fit in your robot because other parts are standing in the way, you might
want to use an <A HREF="https://www.reichelt.de/Adapter-Gender-Changer/DELOCK-65593/3/index.html?GROUPID=6062&ARTICLE=157596">adapter</A> and/or
an <A HREF="https://www.reichelt.de/Sub-D-Kabel/DELOCK-84064/3/index.html?ARTICLE=179872&GROUPID=6082">extension cable</A>
in order to connect the module properly.
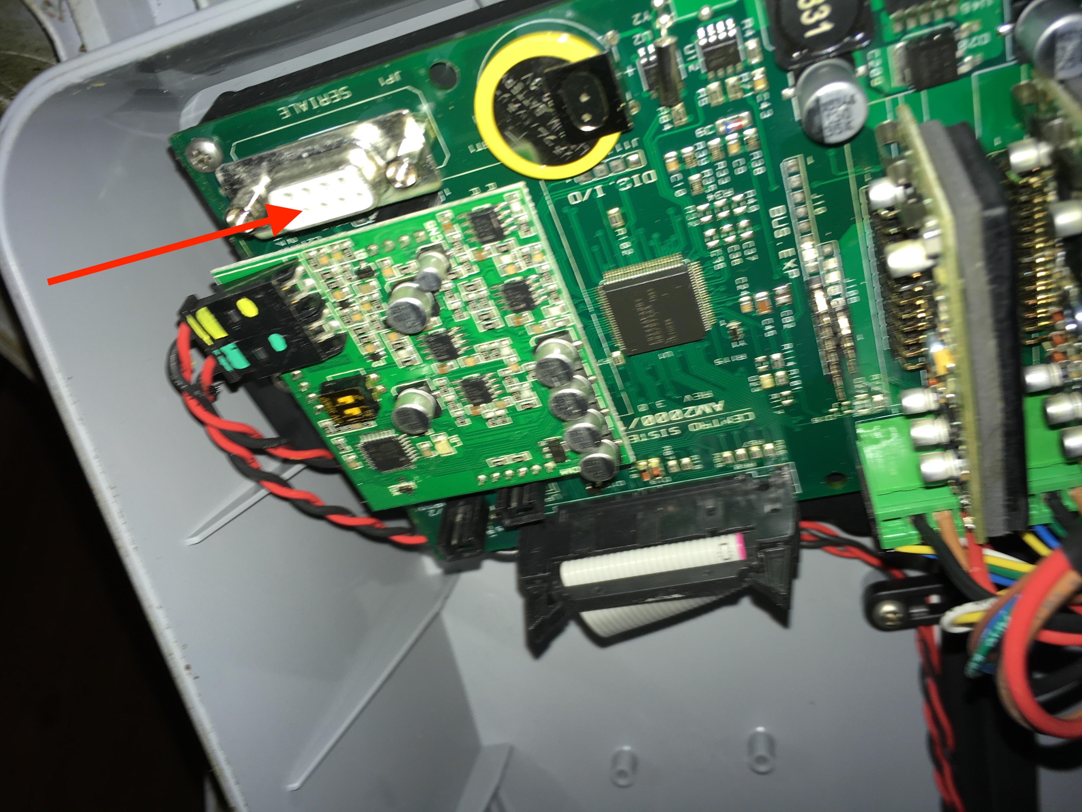
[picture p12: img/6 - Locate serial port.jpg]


If you want, you can use the screws of the bluetooth module to also fixate the Robotan module:
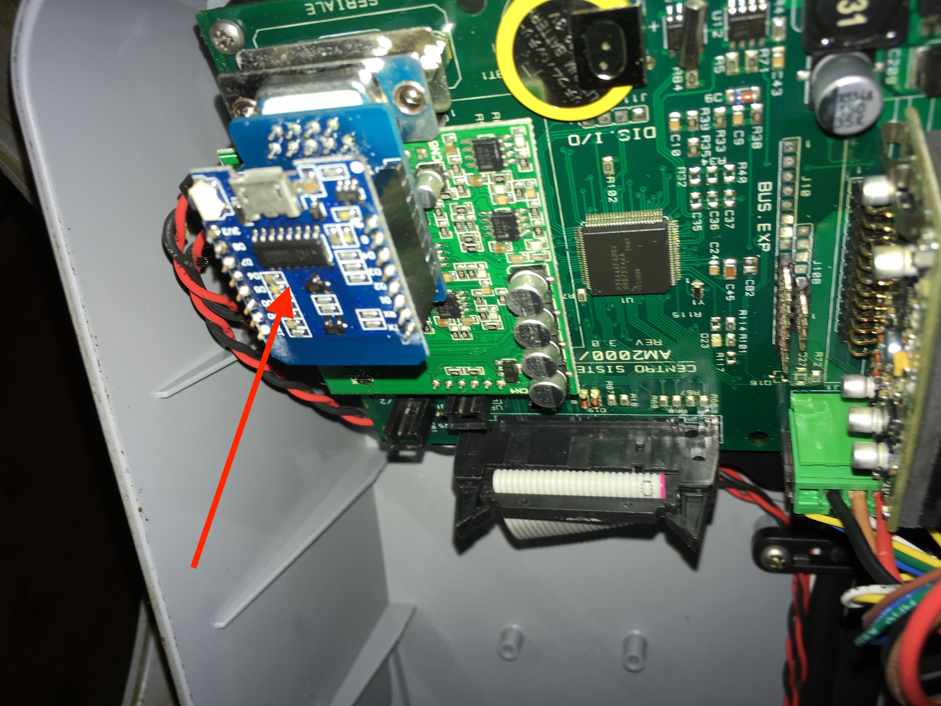
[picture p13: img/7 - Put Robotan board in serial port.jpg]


<H3>Done :-)!</H3>

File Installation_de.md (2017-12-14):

<H2>Installation</H2>
English version can be found <A HREF="Installation.md">here</A>.  
<BR><BR>
Die Installation des Robotan Boards ist nicht besonders schwer, aber bitte beachte, dass es sich hierbei nicht um ein offizielles Produkt von Zucchetti oder eines anderen Rasenmähroboterherstellers handelt.<BR>
DESWEGEN ERLISCHT DIE GARANTIE BEIM EINBAU! Bitte also nur dann mit dem Einbau fortfahren, wenn man sich dieser Konsequenz bewusst ist!

Die gezeigten Fotos stammen von einem Herkules Wiper Ciiky XH2 (baugleich mit dem Ambrogio L30 oder Stiga Autoclip 228S. 
Falls Du also ein anderes Modell hast, können die Positionen der Schrauben unterschiedlich sein. Frage Deinen Händler oder in einem Forum nach, wenn Du Dir unsicher bist!

<H3>Öffnen des Roboters</H3>
Zuerst den Roboter umdrehen, so dass man die Unterseite sehen kann, wo man die
zwei Plastikabdeckungen finden muss, die die unteren beiden Schrauben abdecken.


Dann muss man diese Plastikabdeckungen mit einem flachen Schraubenzieher
hochhebeln. Dabei unbedingt aufpassen, dass man sich dabei nicht an den
Klingen des Roboters verletzt!


Nun die beiden Schrauben herausdrehen. Es kann sein, dass sich diese nicht 
komplett herausdrehen lassen, das ist aber in Ordnung.


Jetzt den Roboter wieder umdrehen und die beiden Torx-Schrauben auf der hinteren
Seite des Roboters ausfindig machen und herausdrehen. Es kann sein, dass sich
diese ebenfalls nicht komplett herausdrehen lassen, das ist aber in Ordnung.
Du musst nur in der Lage sein die beiden Druckflächen über den Schrauben so weit
hereindrücken zu können, dass sich die Abdeckung hochheben lässt.
Beim Hochheben der Abdeckung diese nicht zu weit öffnen, ansonsten könnten
die Verbindungskabel zwischen Display und Mainboard herausgezogen werden! 5-10cm
Öffnung sind ausreichend.


<H3>Installation des Robotan Boards</H3>

Finde das Bluetooth Modul, falls dieses installiert sein sollte. Ansonsten fahre
mit dem nächsten Schritt fort. Entferne das Bluetooth Modul und bewahre es gut
auf, da Du es auch zukünftig brauchst, wenn Du über die App Deines Roboters
ein Firmware-Update des Roboters über Bluetooth durchführen musst.  
Um das Modul zu entfernen, musst Du zwei Schrauben entfernen, die das Modul am 
Mainboard fixieren. Sie befinden sich direkt unter den runden Löchern des Moduls
(siehe blaue Pfeile):


Lokalisiere den leeren seriellen Anschluss und stecke das Robotan Board dort ein. 
Wenn der serielle Anschluss bei Deinem Roboter ungünstig liegt und Gehäuseteile
den Einbau des Moduls verhindern, wäre ggf. ein <A HREF="https://www.reichelt.de/Adapter-Gender-Changer/DELOCK-65593/3/index.html?GROUPID=6062&ARTICLE=157596">Winkeladapter</A>
und/oder ein <A HREF="https://www.reichelt.de/Sub-D-Kabel/DELOCK-84064/3/index.html?ARTICLE=179872&GROUPID=6082">Verlängerungskabel</A> hilfreich.


Wenn Du möchtest, kannst Du die Schrauben des Bluetooth Moduls dafür benutzen,
um das Robotan Board zu fixieren:


<H3>Fertig :-)!</H3>

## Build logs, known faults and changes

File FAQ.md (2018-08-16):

<H2>Frequently Asked Questions (FAQ)</H2>
Die deutsche Version findet man <A HREF="FAQ_de.md">hier</A>.
<H3>Where can I get support?</H3>
The following forum is currently used to discuss the development of Robotan and (limited) support can be given there as well:<BR>
  http://www.roboter-forum.com/showthread.php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
<H3>I'm trying to connect to the "Robotan" WiFi network, what is the password?</H3>
  <code>Robotan88</code>
<H3>I want to access the Robotan website, what is the username and password?</H3>  
Unless you have specified your own credentials during installation, these are the defaults:  <BR>
Username: <code>Robotan</code>  <BR>
Password: <code>Robotan88</code>
<H3>Can I update my robot firmware with Robotan?</H3>
No, unfortunately not. But with an added Bluetooth module (HC-05 or HC-06, less than 10 Euros), Robotan can act as a standard Bluetooth device that is discoverable by Android devices, and these can be used to update the robot's firmware.<BR>
Please take note that this will unfortunately not work with iOS devices because Apple requires all Bluetooth modules to be registered with them before they can be used. And this is not the case with readily available Bluetooth modules.
<H3>How do I need to configure the Bluetooth module?</H3>
The device speed has to be set to 38400 bps, 8 data bits, 1 stop bit, no parity. The bluetooth PIN code must be set to 0000.<BR>
If you install the module and run the provided <code>RobotanBT.ino</code>, it should configure the module for you. Please take note that you may have to put the module into programming mode by pressing a micro-switch or short-circuit two pins during powering up the module. Refer to the module's instructions for further details.
<H3>Why is the source code of Robotan not available?</H3>
As you can see with my other projects, I'm a supporter of open source software. However, with this project, I had to figure out how the app and the robot communicate with each other. This is legal (at least here in Germany), but it may not be legal to tell the world how this protocol works. And this would be the case if I make the source code available, because everyone (with a little bit of programming knowledge) would be able to find out in no time. And as I'm the type of guy who rather is safe than sorry, the core Robotan program can only be downloaded as bin image.

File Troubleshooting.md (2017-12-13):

<H2>Troubleshooting</H2>
Die deutsche Version findet man <A HREF="Troubleshooting_de.md">hier</A>.
<H3>I'm asked for a username and password!</H3>
The username is <code>Robotan</code>, the password is <code>Robotan88</code>
<H3>I can't open the Robotan website</H3>
There could be several reasons:

1. Make sure Robotan and you are in the same WiFi network. If you have configured Robotan to use your own network, but in the list of
WiFi networks, a network called "Robotan" still shows up, that means that Robotan was unable to connect to your WiFi network.
Connect to the Robotan WiFi network and check the configuration.

2. You are too far away from the robot. Get closer and try again. If this occurs in large(r) parts of your garden, you might want to get 
a WiFi repeater.
<H3>I can't flash the firmware using the Arduino IDE</H3>
Please make sure that the Robotan board is not attached to the Wemos D1 Mini when flashing the initial firmware via USB!

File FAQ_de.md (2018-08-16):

<H2>Frequently Asked Questions (FAQ)</H2>
English version can be found here <A HREF="FAQ_de.md">here</A>.
<H3>Wo kann ich Hilfe bekommen?</H3>
Das folgende Forum ist momentan der Platz, um die Entwicklung von Robotan und
(begrenzter) Support kann dort gegeben werden:<BR>
  http://www.roboter-forum.com/showthread.php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
<H3>Ich versuche mich, mit dem "Robotan" WLAN zu verbinden, wie lautet das
Passwort?</H3>
  <code>Robotan88</code>
<H3>Ich möchte die Robotan webseite aufrufen, wie lauten die Zugangsdaten?</H3>  
Falls während der Installation keine individuellen Zugangsdaten konfiguriert wurden, lauten diese standardmäßig:  
Username: <code>Robotan</code>  <BR>
Password: <code>Robotan88</code>
<H3>Kann ich mit Robotan die Firmware meines Mähers updaten?</H3>
Nein, leider nicht. Aber mit dem Anschluss eines Bluetooth-Moduls 
(HC-05 oder HC-06, weniger als 10 Euro), kann Robotan als Bluetooth-Gerät
agieren, das von Android-Geräten erkannt wird, von dem aus man dann mit der
entsprechenden App ein Update ausführen kann.<BR>
Bitte beachte, dass dies leider nicht mit iOS-Geräten funktioniert, weil
Apple es erfordert, dass alle Bluetooth-Geräte vorher lizenziert werden. 
Und das ist bei diesen Standard-Modulen nicht der Fall.
<H3>Wie muss ich das Bluetooth-Modul konfigurieren?</H3>
Das Modul muss auf 38400bps, 8 Datenbits, 1 Stoppbit und keine Parität 
konfiguriert werden. Der Bluetooth PIN-Code muss auf 0000 gesetzt sein.<BR>
Wenn Du das Modul installierst und die <code>RobotanBT.ino</code> auf dem Wemos D1 
aufspielst, sollte das Modul richtig konfiguriert werden.<BR>
Bitte beachte, dass das Bluetooth-Modul im Programmiermodus sein muss. Dafür
muss man je nach Modul entweder beim Einschalten einen Microschalter drücken
oder zwei Pins kurzschließen. Genauere Infos dazu stehen in der Anleitung zu
dem jeweiligen Modul.
<H3>Warum ist der Sourcecode für Robotan nicht verfügbar?</H3>
Wie Du bei meinen anderen Projekten sehen kannst, bin ich ein Unterstützer
der Open Source Philsophie. Für dieses Projekt musste ich aber herausfinden,
wie die App und der Roboter miteinander kommunizieren. Das ist legal
(zumindest hier in Deutschland), aber es ist möglicherweise nicht legal der Welt
zu erzählen, wie dieses Protokoll im Detail aussieht, Und das wäre der Fall, wenn
ich den Sourcecode öffentlich machen würde, weil jede/r, der/die sich den Code 
mit etwas Programmierkenntnis ansehen würde, diese Information in kürzester
Zeit bekommen würde.  
Und da ich der Typ Mensch bin, die lieber auf Nummer sicher gehen, kann das 
Kernprogramm der Robotan Software nur als Binär-Image heruntergeladen werden.

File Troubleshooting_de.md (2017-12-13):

<H2>Troubleshooting</H2>
English version can be found  <A HREF="Troubleshooting.md">here</A>.
<H3>Ich werde nach einem Usernamen und Password gefragt!</H3>
Der Username ist <code>Robotan</code>, das Password ist <code>Robotan88</code>
<H3>Ich kann die Robotan Weibseite nicht öffnen!</H3>
Dies kann mehrere Gründe haben:  

1. Stelle sicher, das Robotan und Du im gleichen WLAN-Netzwerk sind. Wenn Du
Robotan so konfiguriert hast, dass er Dein WLAN mitbenutzen soll, Du aber immer
noch ein WLAN-Netz mit Namen "Robotan" siehst, bedeutet dass, das Robotan nicht
in der Lage war, sich in Deinem WLAN anzumelden. Verbinde Dich in dem Fall mit
dem Robotan WLAN und überprüfe die Konfiguration.

2. Du bist zu weit weg vom Roboter. Nähere Dich dem Roboter und versuche es 
noch einmal. Wenn dies in einem (größeren) Teil Deines Gartens passiert, 
müsstest Du über den Kauf eines WLAN-Repeaters nachdenken.

<H3>Ich kann die Firmware nicht mit der Arduino IDE flashen</H3>
Wenn Du die initiale Firmware auf den Wemos D1 Mini flashen möchtest, darf
das Robotan Board dabei nicht auf den Wemos aufgesteckt sein!

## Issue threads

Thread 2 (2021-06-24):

'End Time' earlier than 'Start Time' crashes mower while charging

freddieleeman, 2021-06-24:
If you set the `End Time` earlier than the `Start Time` or the `Start Time` later than the `End Time` the mower crashes (**CODE 201 PLEASE RESTART**) and Robotan gets disconnected. The only way to resolve this issue is to disconnect the mower from the charger , reboot the mower, and fix the time values.

Suggested fix:
Saving new value to Start: if `value` > `end`: change `end` to **23:59** before changing `start` to `value`
Saving new value to End: if `value` < `start`: change `start` to **00:00** before changing `end` to `value`

This way, a user can alter both time settings without paying attention to the current values.

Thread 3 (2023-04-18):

firmware version is to low?

freddieleeman, 2023-04-18:
Recently I'm started seeing the following error on the status page:

`Attention: Your firmware version is too low (<41000) to display all possible parameters, please update your firmware!`

I've installed Robotan on an Ambrogio L30 ELITE (Robot 7030EL0) running r53714. Removing the mower from the charging station and restarting it appears to resolve the issue. Anyone seen this error before and knows what might be causing it?

freddieleeman, 2023-05-05:
It is possible that the problem began when I upgraded from a D1 mini to a D1 mini pro to extend the WiFi range using an external antenna. However, after some troubleshooting, I believe I have fixed the issue by disconnecting the CP2104 USB to UART bridge as shown here: https://community.home-assistant.io/t/mitsubishi-ac-with-wemos-d1-mini-pro/107007/147.

Closed 2023-05-05.

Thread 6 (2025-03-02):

Robotan FHEM

interceptor70, 2025-03-02:
Hallo ich habe das Modul [98_Robotan.pm](https://github.com/fredlcore/Robotan/blob/master/98_Robotan.pm)
installiert aber ich nutze den Mähspitzel - Wi-Fi für Robomow
und das ist glaube ich die gleiche version..

Jetzt die Wilde Frage gibt es auch eine Mähspitzel - Wi-Fi für Robomow version des 98_Robotan.pm ?

Lg Gerrit

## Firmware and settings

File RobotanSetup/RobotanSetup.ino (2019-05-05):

/*
  To upload through terminal you can use: curl -u Robotan:Robotan88 -F "image=@fRobotan.ino.bin" robotan.local:8080/update
  Adjust credentials in case you changed them from default.
*/

/* 
    By default this script will become an AP and spawn a new WLAN network.
    The default network name is "Robotan" and the WiFi password is "Robotan88" (without quotation marks).
   
    If you provide your WLAN local network SSID / password information, the script will first try to connect to your 
    existing local WLAN network as a client. Upon success, local WLAN credentials will be stored in the EEPROM and the robotan
    firmware will connect after flashed and restarted.Only if the local WLAN connection is unsuccessful, the script will revert to default behavior 
    
    If you decide to change the default username / password (recommended), the new values will be copied to the Wemos EEPROM 
    and be active after the robotan firmware file has been flashed and restarted. 

    Thanks to Oliver Weismantel for helpful additions!
*/ 

#define LOGIN_CREDENTIALS_LENGTH_MAX 16

/* begin configuration section */
const char WLAN_local_SSID[32] = "";       // fill in your existing local WLAN SSID
const char WLAN_local_password[63] ="";    // fill infor your existing local WLAN password

const char http_username[LOGIN_CREDENTIALS_LENGTH_MAX + 1] = "Robotan";    // HTTP username, maximum of 16 characters
const char http_password[LOGIN_CREDENTIALS_LENGTH_MAX + 1] = "Robotan88";  // HTTP password, maximum of 16 characters
/* end configuration section */

#include <ESP8266WiFi.h>
#include <WiFiClient.h>
#include <ESP8266WebServer.h>
#include <ESP8266HTTPUpdateServer.h>
#include <EEPROM.h>
extern "C" {
  #include "user_interface.h"
}

const char* host = "robotan";
const char* def_ssid = "Robotan";
const char* def_pass = "Robotan88";

int eeprom_allocated_mem = 4096;
int eeprom_login_credentials_base=512;

ESP8266WebServer httpServer(8080);
ESP8266HTTPUpdateServer httpUpdater;
WiFiClient WLAN_Client;
IPAddress local_ip;

void setup(void) {

  /* Initialize Serial Port */
  Serial.begin(38400);
  Serial.println();

  /* Clear EEPROM */
  Serial.print("Clearing EEPROM...");
  EEPROM.begin(eeprom_allocated_mem);
  for (int i = 0; i < eeprom_allocated_mem; ++i) { 
      EEPROM.write(i, 0); 
  }
  Serial.println("done");

  /* Store http username / password in EEPROM */
  EEPROM.put(eeprom_login_credentials_base, http_username);
  EEPROM.put(eeprom_login_credentials_base +  LOGIN_CREDENTIALS_LENGTH_MAX, http_password);

  Serial.println("Setting up Firmware Upload Tool...");
  
  if (!Local_WLAN_Connect()) {
    /* default behavior - spawn access point */
    WiFi.mode(WIFI_AP);  
    wifi_station_set_hostname((char*)"robotan");
    WiFi.softAP(def_ssid, def_pass);
    Serial.printf("Created WLAN access point with WLAN SSID %s\n",def_ssid);
    /* local IP */
    local_ip = WiFi.softAPIP();
    Serial.printf("\n>>> Connect to WiFi network \"%s\" with password \"%s\"\n\n",def_ssid, def_pass);
  }
  
  EEPROM.commit();
  EEPROM.end();
  
  /* Start Update Server Process */
  httpUpdater.setup(&httpServer);
  httpServer.begin();

 /* Ready */
  Serial.printf("\n>>> HTTPUpdateServer ready!\n>>> Open http://");
  Serial.print(local_ip);
  Serial.print(":8080/update in your browser to upload the Robotan firmware.\n");

  return;
}

void loop(void){
  httpServer.handleClient();
}


boolean Local_WLAN_Connect() {
  /* Try local WLAN using credentials given */
  if ( strlen(WLAN_local_SSID) && strlen(WLAN_local_password)) {
    /* Wifi client mode */
    WiFi.mode(WIFI_STA);
    
    /* connect to existing WLAN */
    Serial.printf("Connecting to local WLAN SSID %s",WLAN_local_SSID);
    WiFi.begin(WLAN_local_SSID, WLAN_local_password);

    /* Wait for connection to be successful */
    for (int i=0; i<20; i++) {  //timeout [s]
      delay(1000);  
      
      int connectionStatus = WiFi.status();
      switch(connectionStatus) {
        case WL_CONNECTED: 
          Serial.println("...connected");
          local_ip = WiFi.localIP();
          /* store WiFi credentials in EEPROM */
          EEPROM.put(0,WLAN_local_SSID);
          EEPROM.put(32,WLAN_local_password);
          return true; // WLAN connection successful
        default:
          Serial.print(".");
      }
    }
  }
  Serial.println("...unable to connect"); // revert to default behavior
  return false;
}

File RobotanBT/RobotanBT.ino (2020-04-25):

#include <SoftwareSerial.h>

const uint32_t baud_rates[] = {9600, 38400, 57600, 115200};

SoftwareSerial BluetoothSerial;

void setup(void) {
  Serial.begin(38400);

  for (int x = 0; x < 4; x++) {    
    BluetoothSerial.begin(baud_rates[x], SWSERIAL_8N1, 2, 0, false, 256);
    Serial.print("\nRobotan Bluetooth module configuration starts at ");
    Serial.println(baud_rates[x]);
    BluetoothSerial.println("AT+NAME=\"Robot\"");
    delay(500);
    BluetoothSerial.println("AT+NAME=Robot");
    delay(500);
    BluetoothSerial.println("AT+NAMERobot");
    delay(500);
    BluetoothSerial.println("AT+UART=38400,0,0");
    delay(500);
    BluetoothSerial.println("AT+BAUD6");
    delay(500);
    BluetoothSerial.println("AT+PIN000000");
    delay(500);
    BluetoothSerial.println("AT+PSWD=\"0000\"");
    delay(500);
    BluetoothSerial.println("AT+PIN0000");
    delay(500);
    BluetoothSerial.println("AT+ADDR");
    delay(500);
    BluetoothSerial.println("AT+RESET");
    delay(500);
    BluetoothSerial.end();
  }
  Serial.println("\nRobotan Bluetooth module configuration finished.");

  BluetoothSerial.begin(38400);

}

void loop(void) {
  while (BluetoothSerial.available() > 0) {
    Serial.write(BluetoothSerial.read());
    yield();
  }
  while (Serial.available() > 0) {
    BluetoothSerial.write(Serial.read());
    yield();
  }

}

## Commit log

2017-11-11 Bugfixes in board layout
    [Robotan.brd, Robotan.sch]
2017-12-08 Arduino Settings
2017-12-08 Create Assembly Instructions
2017-12-08 Rename Assembly Instructions to Assembly Instructions.md
2017-12-08 Update Assembly Instructions.md
2017-12-12 Update Assembly Instructions_de.md
2018-01-02 New screenshot from Arduino IDE with ESP core 2.4.0
2018-03-01 Added instructions for additional capacitator
2018-04-11 Switched to table layout
2018-06-09 Very important bugfix plus Bluetooth and joystick steering dunctionality
2018-10-08 Add FHEM set commands
    Add FHEM set commands:
    set <device> Start_Time_2
    set <device> End_Time_2
2019-03-13 Removed due to commercial abuse
    [Robotan.brd]
2019-05-09 Updated capacitator value
2019-05-20 Added support for ADXL335 accelerometer; important bugfixes
2019-05-23 Added instructions for ADXL335 acceleration sensor
2019-05-23 Added instructions for ADXL335 sensor
2019-06-04 Support for ADXL335 and KY-003 sensors
2019-06-04 Updated instructions for ADXL335 and KY-003 sensors
2019-06-04 Added instructions for ADXL335 and KY-003 sensors
2019-06-09 Bugfix for acceleration sensor configuration
2019-07-16 Added keyboard controls for steering: left/right arrow, P for pause, S for spiral, H/W for Home/Work
2020-04-30 Added notice for older stable version in case firmware update via Bluetooth fails
2020-05-10 New board layout
2020-05-10 Adjusted to new board layout
2020-05-10 Adjusted to newer board version
